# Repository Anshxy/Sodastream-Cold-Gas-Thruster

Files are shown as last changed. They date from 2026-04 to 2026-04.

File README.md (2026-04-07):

# CO2 Cold Gas Thruster — Design, CFD & Physical Test
final

A converging-diverging nozzle designed from first principles for a SodaStream CO2 cylinder, validated in Ansys Fluent, and physically tested. The goal was to run the same system through three levels of analysis and understand where each one breaks down.

---

## Results

| Method | Thrust |
|---|---|
| MATLAB isentropic (ideal) | 1.23 N |
| Ansys Fluent (viscous) | 1.19 N |
| Physical test | 0.75 N |
 
The CFD-to-MATLAB gap is viscous losses — boundary layer growth and non-uniform exit velocity profile. The hardware-to-CFD gap is regulator droop (6 bar set point, 5.5 bar delivered under flow demand), resin printed surface roughness, and CO2 deviating from ideal gas behaviour at ~155 K exit temperature.

---

| Parameter | Value |
|---|---|
| Propellant | CO2 |
| Inlet pressure (design) | 6 bar |
| Inlet pressure (measured) | 5.5 bar |
| Throat diameter | 1.5 mm |
| Exit Mach number | 1.84 |
| Diverging half angle | 5° |
| Converging half angle | 30° |
| Exit temperature | ~155 K |
| Mass flow rate | ~3 g/s |
| Burn duration (425g cylinder) | ~141 s |

---

## Analytical Model (MATLAB)

Sim1_Analysis

- Mach number distribution along the nozzle centreline from the isentropic solver. The throat sits at x = 0, subsonic flow on the left, supersonic on the right. Solved using fzero on both branches of the area-Mach relation.
- Thrust as a function of inlet pressure from 1 to 6 bar. Shows how performance degrades as the cylinder depletes. The design point sits at the top left of the curve.

---

## CFD (Ansys Fluent)

final

mach number cd nozzle

Temp

2D axisymmetric simulation in Ansys Fluent 2025 R2. k-omega SST turbulence model, CO2 ideal gas, pressure inlet at 6 bar stagnation, pressure outlet at 101,325 Pa. Exit Mach number consistent with analytical prediction at 1.84.

The boundary layer is visible along the diverging wall. CFD exit velocity came in at 388 m/s versus the theoretical 396 m/s — the 8 m/s difference accounts for the 0.04 N gap between MATLAB and Fluent predictions.

---

## Physical testing

https://github.com/user-attachments/assets/d54a0f28-d8d5-481c-8475-6a8e69996e40

Tested at 5.5 bar measured inlet pressure (set point 6 bar, drooped under ~3 g/s flow demand). Thrust measured at 0.75 N. Visible CO2 frost formed on the nozzle body during firing consistent with the predicted 155 K exit temperature.

---

## Hardware
 
- SodaStream 425g CO2 cylinder
- KegLand deluxe SodaStream adapter
- KegLand MK4 dual gauge regulator 
- PETG printed nozzle 

## Notes
 
Basically, the MATLAB model gave me the absolute best-case scenario. The real world is never that perfect. I didn't run all three methods expecting the thrust numbers to match perfectly; I just wanted to see exactly how much performance I was losing at each step and figure out which physical mechanisms (like friction) were causing it.

Setup for the Ansys Fluent 2025 R2 simulation was pretty standard: 2D axisymmetric, k-omega SST, and ideal gas CO2.

## Author

Ansh Rawat
Adrian Jalgha

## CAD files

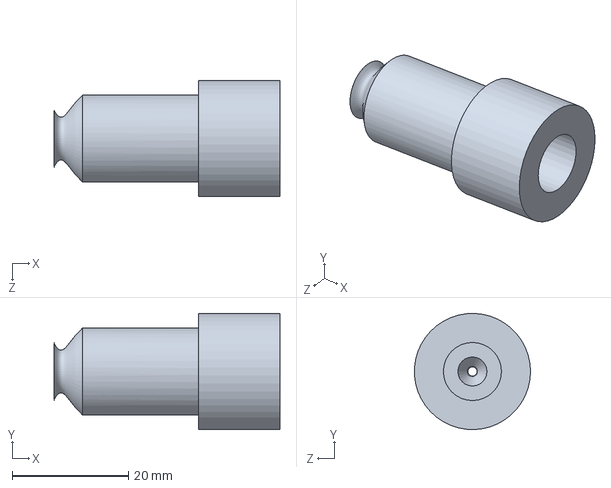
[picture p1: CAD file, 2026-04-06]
CAD/CD Nozzle.SLDPRT
38.9 x 20.0 x 20.0 mm
